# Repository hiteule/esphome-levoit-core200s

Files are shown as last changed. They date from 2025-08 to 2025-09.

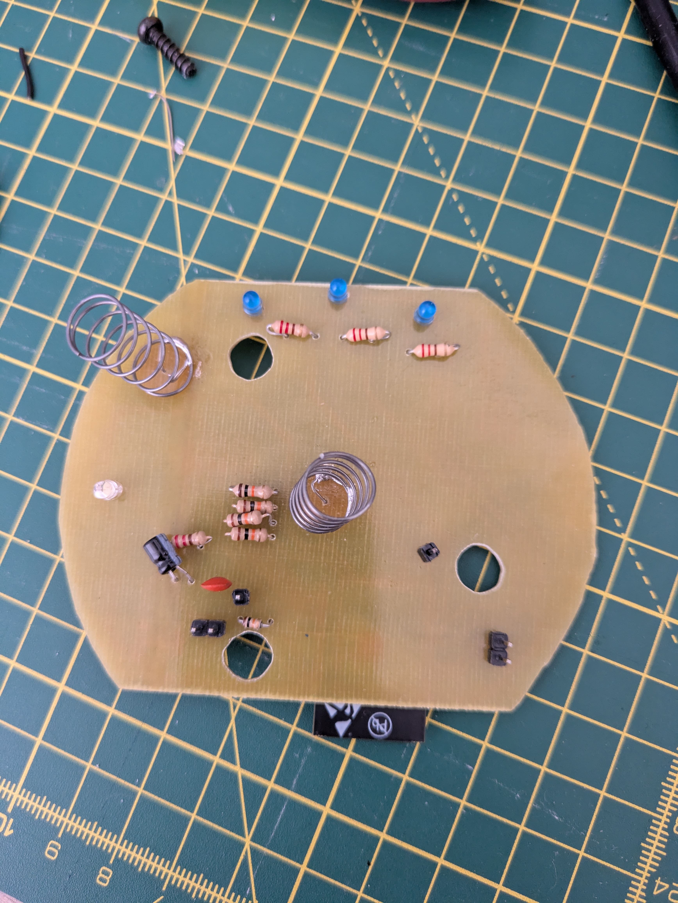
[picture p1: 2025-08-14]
pcb/pcb-front.jpg

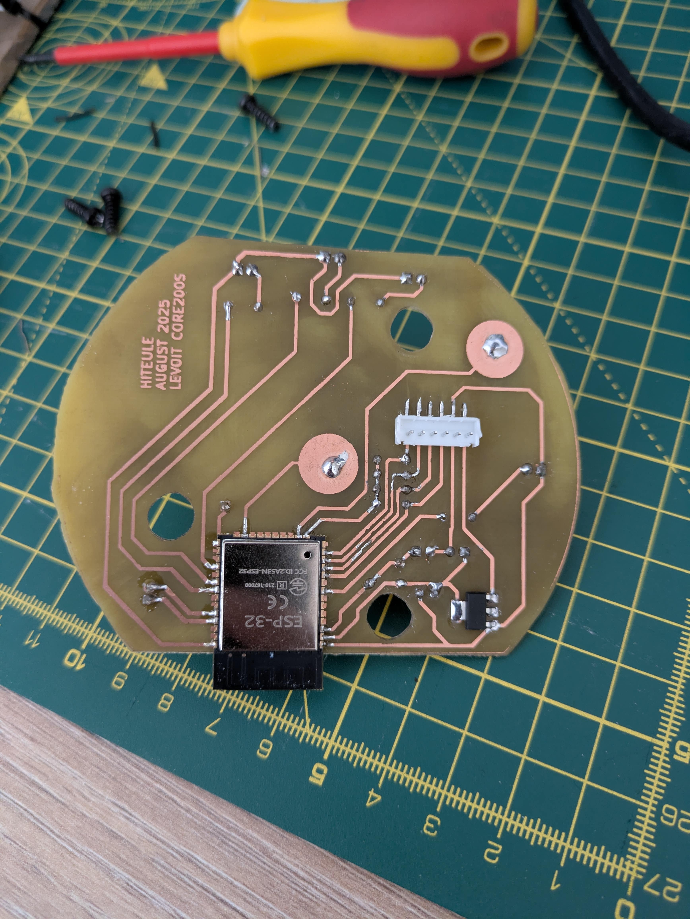
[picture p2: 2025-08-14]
pcb/pcb-back.jpg

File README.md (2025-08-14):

# ESPHome Levoit Core200s

An electronic board designed to replace the Levoit Core 200s air purifier control board (because I broke it).
Only the "Fan speed" and "Power" buttons are functional.
The air purifier is exposed via [ESPHome], which enables integration with [HomeAssistant].

## PCB

The board must be connected to the "power board" of the air purifier via the JST connector on J1.
This connector supplies 5V on pin 1. Take care to connect it the right way.

The ESP32 should be flashed with ESPHome via J2(TX), J3(RX), J6(RTS), J7(DTR) J8(3.3V), J9(GND).
For this, you can use my [ESP/Atmega programmer].

The card was designed with [Kicad]. The sources (schematic & board) are in the "pcb" folder.

## Software

The ESP32 is exposing the Air Purifier in Home Assisant. To do it, we use [ESPHome].
To do so:
* Install the ESPHome module on [HomeAssistant].
* Plug the board to your computer with J2(TX), J3(RX), J6(RTS), J7(DTR) J8(3.3V), J9(GND) and the [ESP/Atmega programmer].
* In the ESPHome module, create a new device.
* Update your ESPHome device with the `levoit-core200s.yaml` file.
* Install it on the ESP.

Now you can unplug the ESP from your computer, install it into the air purifier and connect it via J1.
ESP should boot normally and the air purifier should be visible in [HomeAssistant].

[HomeAssistant]: https://www.home-assistant.io
[ESPHome]: https://esphome.io/
[ESP/Atmega programmer]: https://github.com/hiteule/programmer-esp-atmega
[Kicad]: https://www.kicad.org

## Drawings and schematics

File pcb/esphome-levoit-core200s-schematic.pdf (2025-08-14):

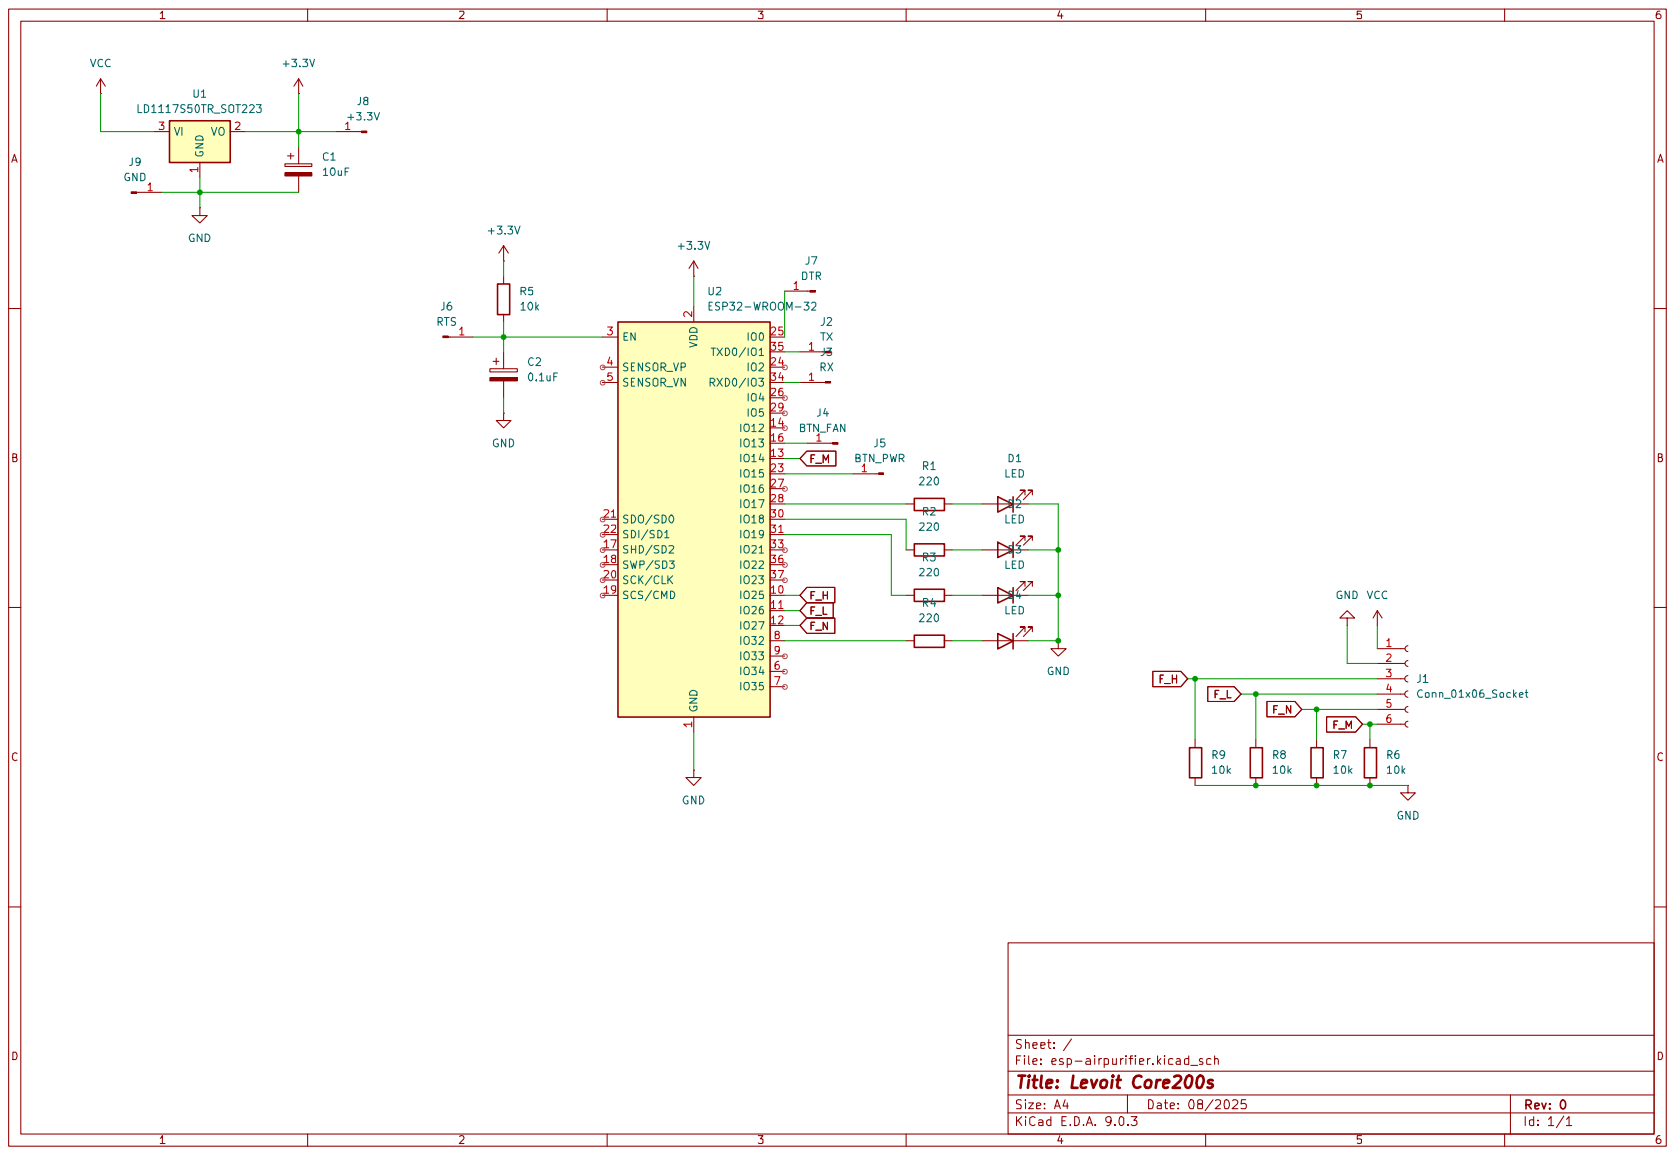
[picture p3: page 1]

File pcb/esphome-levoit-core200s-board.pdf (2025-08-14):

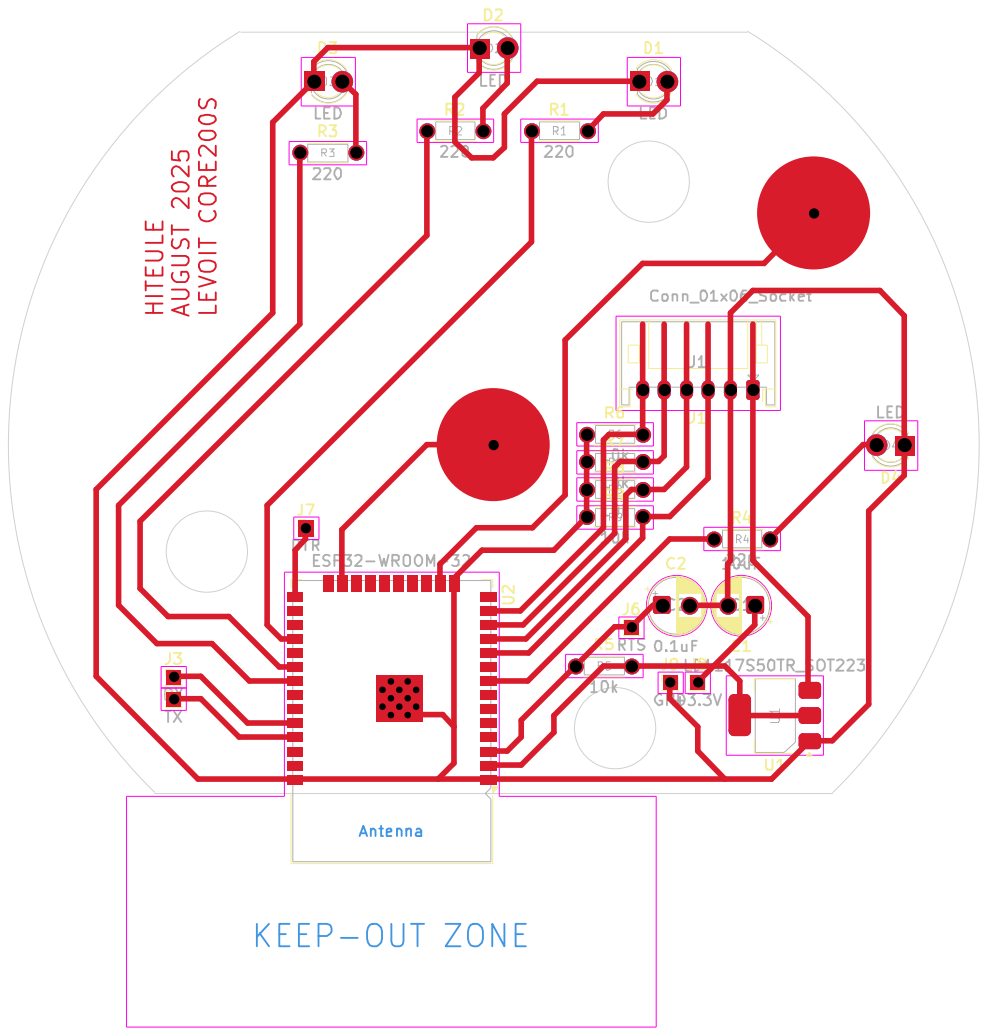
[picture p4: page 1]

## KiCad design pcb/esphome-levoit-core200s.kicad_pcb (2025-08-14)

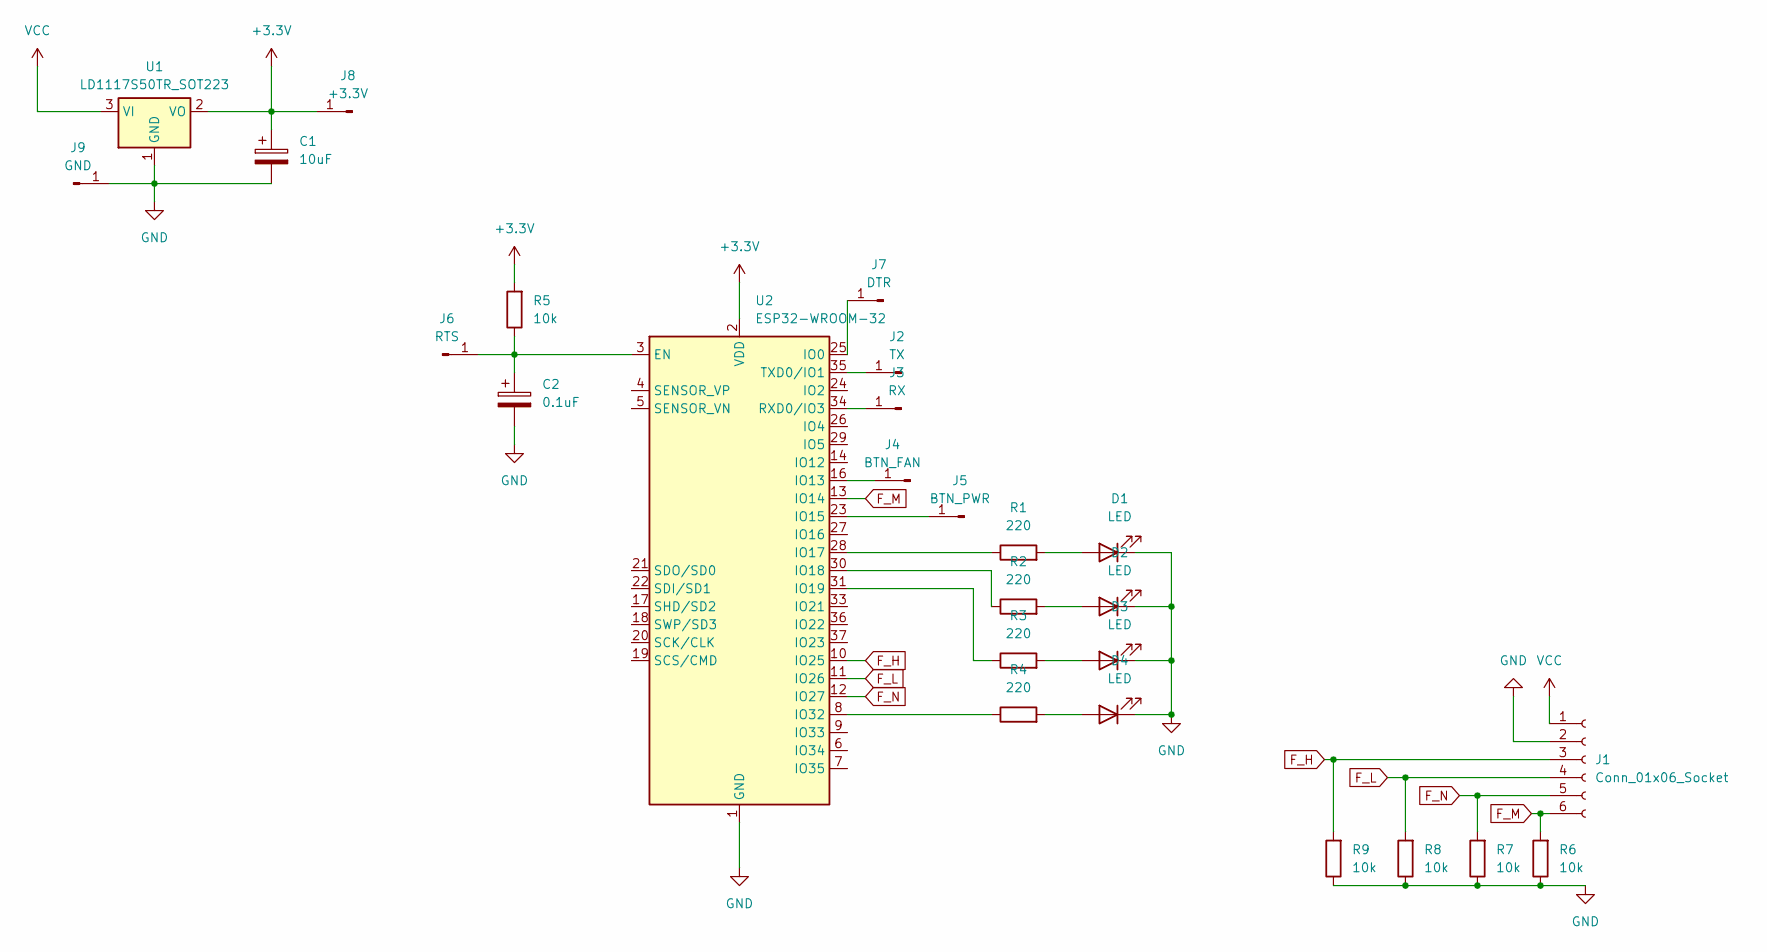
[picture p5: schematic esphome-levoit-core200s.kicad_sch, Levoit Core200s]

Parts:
C1: 10uF; CP_Radial_D5.0mm_P2.50mm
C2: 0.1uF; CP_Radial_D5.0mm_P2.50mm
D1, D2, D3, D4: LED; LED_D3.0mm
J1: Conn_01x06_Socket; JST_PH_S6B-PH-K_1x06_P2.00mm_Horizontal
J2: TX; PinHeader_1x01_P1.00mm_Vertical
J3: RX; PinHeader_1x01_P1.00mm_Vertical
J4: BTN_FAN; PinHeader_1x01_P1.00mm_Vertical
J5: BTN_PWR; PinHeader_1x01_P1.00mm_Vertical
J6: RTS; PinHeader_1x01_P1.00mm_Vertical
J7: DTR; PinHeader_1x01_P1.00mm_Vertical
J8: +3.3V; PinHeader_1x01_P1.00mm_Vertical
J9: GND; PinHeader_1x01_P1.00mm_Vertical
R1, R2, R3, R4: 220; R_Axial_DIN0204_L3.6mm_D1.6mm_P5.08mm_Horizontal
R5, R6, R7, R8, R9: 10k; R_Axial_DIN0204_L3.6mm_D1.6mm_P5.08mm_Horizontal
U1: LD1117S50TR_SOT223; SOT-223-3_TabPin2
U2: ESP32-WROOM-32

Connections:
+3.3V: C1.1, J8.1, R5.2, U1.2 (VO), U2.2 (VDD)
F_H: J1.3, R9.2, U2.10 (IO25)
F_L: J1.4, R8.2, U2.11 (IO26)
F_M: J1.6, R6.2, U2.13 (IO14)
F_N: J1.5, R7.2, U2.12 (IO27)
GND: C1.2, C2.2, D1.1 (K), D2.1 (K), D3.1 (K), D4.1 (K), J1.2, J9.1, R6.1, R7.1, R8.1, R9.1, U1.1 (GND), U2.1 (GND), U2.15 (GND), U2.38 (GND), U2.39 (GND)
unnamed: D1.2 (A), R1.2
unnamed: D2.2 (A), R2.2
unnamed: D3.2 (A), R3.2
unnamed: D4.2 (A), R4.2
unnamed: J2.1, U2.35 (TXD0/IO1)
unnamed: J3.1, U2.34 (RXD0/IO3)
unnamed: J4.1, U2.16 (IO13)
unnamed: J5.1, U2.23 (IO15)
unnamed: C2.1, J6.1, R5.1, U2.3 (EN)
unnamed: J7.1, U2.25 (IO0)
unnamed: R1.1, U2.28 (IO17)
unnamed: R2.1, U2.30 (IO18)
unnamed: R3.1, U2.31 (IO19)
unnamed: R4.1, U2.8 (IO32)
VCC: J1.1, U1.3 (VI)

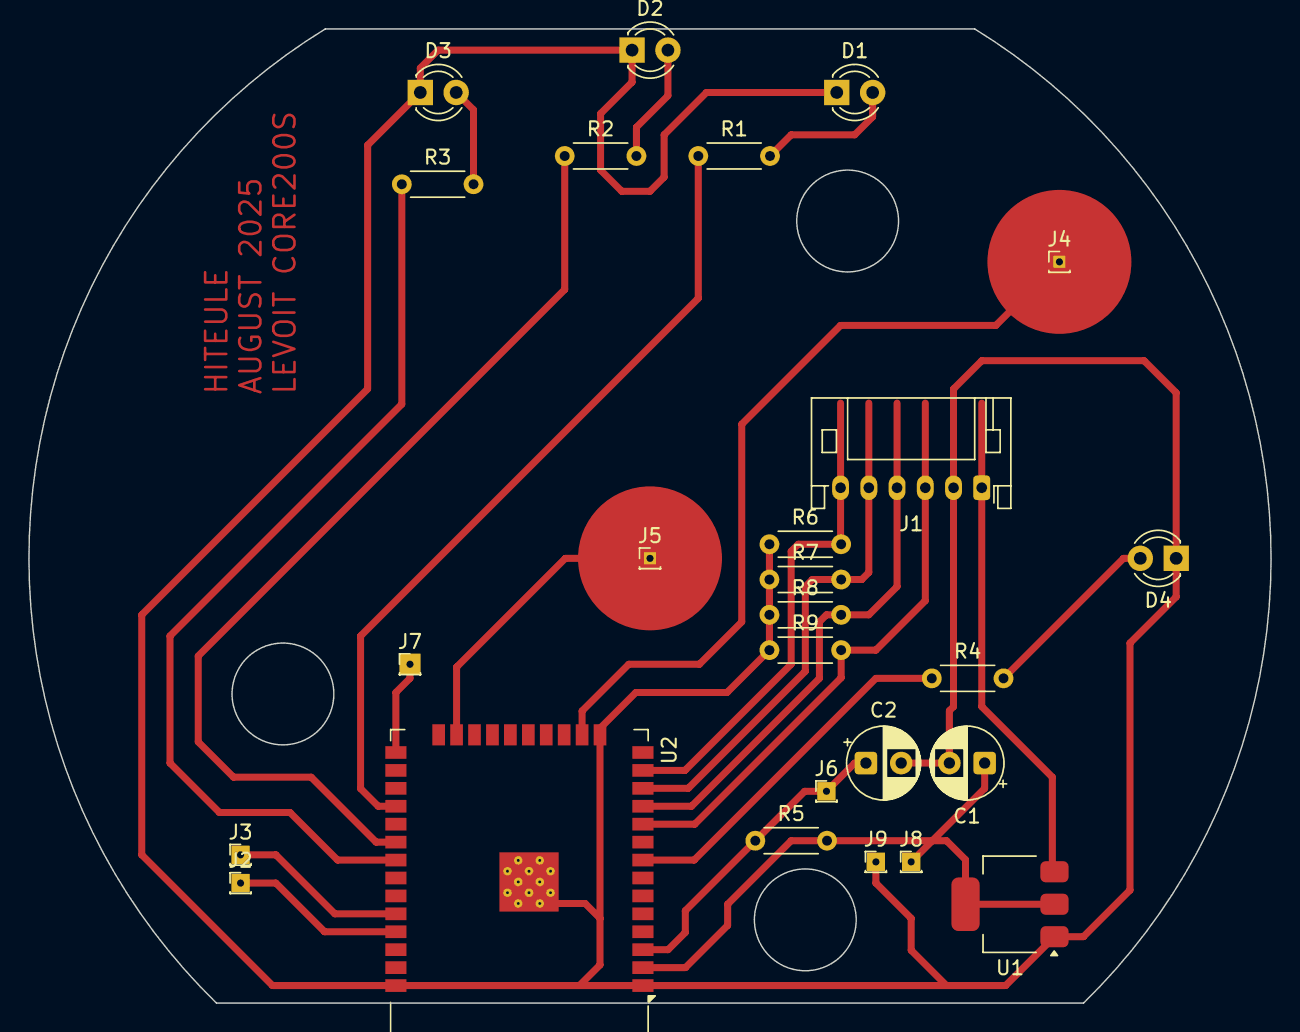
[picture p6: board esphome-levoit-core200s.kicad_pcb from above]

Board: 2 copper layers, 88.0 x 69.0 mm, 26 parts (0 on the bottom side), 21 nets.

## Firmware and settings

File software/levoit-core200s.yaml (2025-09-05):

esphome:
  name: levoit-core200s
  friendly_name: levoit-core200s

esp32:
  board: esp32dev
  framework:
    type: esp-idf

# Enable logging
logger:

# Enable Home Assistant API
api:
  encryption:
    key: "TODO"

ota:
  - platform: esphome
    password: "TODO"

wifi:
  ssid: !secret wifi_ssid
  password: !secret wifi_password

  # Enable fallback hotspot (captive portal) in case wifi connection fails
  ap:
    ssid: "Levoit Core200s Fallback Hotspot"
    password: "TODO"

captive_portal:


external_components:
  - source:
      type: git
      url: https://github.com/hiteule/esphome-levoit-core200s
      ref: master
    components: [ levoit-core200s ]

levoit-core200s:

fan:
  - platform: levoit-core200s
    id: fan_levoit_core200s
    name: Air Purifier
    pin_night: 27
    pin_low: 26
    pin_medium: 14
    pin_high: 25
    pin_led_night: 32
    pin_led_low: 17
    pin_led_medium: 18
    pin_led_high: 19

esp32_touch:
  setup_mode: false

binary_sensor:
  - platform: esp32_touch
    name: "Fan speed"
    pin: GPIO13
    threshold: 1510
    id: btn_fan_speed
    on_press:
      then:
        - fan.cycle_speed:
            id: fan_levoit_core200s
            off_speed_cycle: false
  - platform: esp32_touch
    name: "Fan power"
    pin: GPIO15
    threshold: 1640
    id: btn_fan_power
    on_press:
      then:
        - fan.toggle:
            id: fan_levoit_core200s

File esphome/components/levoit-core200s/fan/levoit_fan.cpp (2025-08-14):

#include "esphome/core/log.h"
#include "levoit_fan.h"

namespace esphome {
namespace levoit {

static const char *const TAG = "levoit-core200s.fan";

void LevoitFan::setup() {
  this->pin_night_->setup();
  this->pin_night_->pin_mode(gpio::FLAG_OUTPUT);
  this->pin_night_->digital_write(false);
  this->pin_low_->setup();
  this->pin_low_->pin_mode(gpio::FLAG_OUTPUT);
  this->pin_low_->digital_write(false);
  this->pin_medium_->setup();
  this->pin_medium_->pin_mode(gpio::FLAG_OUTPUT);
  this->pin_medium_->digital_write(false);
  this->pin_high_->setup();
  this->pin_high_->pin_mode(gpio::FLAG_OUTPUT);
  this->pin_high_->digital_write(false);
  this->pin_led_night_->setup();
  this->pin_led_night_->pin_mode(gpio::FLAG_OUTPUT);
  this->pin_led_night_->digital_write(false);
  this->pin_led_low_->setup();
  this->pin_led_low_->pin_mode(gpio::FLAG_OUTPUT);
  this->pin_led_low_->digital_write(false);
  this->pin_led_medium_->setup();
  this->pin_led_medium_->pin_mode(gpio::FLAG_OUTPUT);
  this->pin_led_medium_->digital_write(false);
  this->pin_led_high_->setup();
  this->pin_led_high_->pin_mode(gpio::FLAG_OUTPUT);
  this->pin_led_high_->digital_write(false);

  this->state = false;
  this->speed = 0;
  this->publish_state();
}

void LevoitFan::dump_config() { LOG_FAN("", "Levoit Fan", this); }

fan::FanTraits LevoitFan::get_traits() {
  // 200s has 4 speeds (night, low, medium, high)
  return fan::FanTraits(false, true, false, 4);
}

void LevoitFan::control(const fan::FanCall &call) {
  bool newPowerState = this->state;

  if (call.get_state().has_value()) {
    newPowerState = *call.get_state();
    
    if (newPowerState) {
      // power on
      this->setFanOff();
      this->pin_low_->digital_write(true);
      this->state = true;
      this->speed = 1;
    } else {
      // power off
      this->setFanOff();
      this->state = false;
      this->speed = 0;
    }
  }

  if (call.get_speed().has_value()) {
    uint8_t targetSpeed = *call.get_speed();

    switch (targetSpeed) {
      case 0:
        // send power off
        this->setFanOff();
        this->state = false;
        this->speed = 0;
        break;
      case 1:
        // speed 1
        this->setFanOff();
        this->pin_night_->digital_write(true);
        this->pin_led_night_->digital_write(true);
        this->state = true;
        this->speed = 1;
        break;
      case 2:
        // speed 2
        this->setFanOff();
        this->pin_low_->digital_write(true);
        this->pin_led_low_->digital_write(true);
        this->state = true;
        this->speed = 2;
        break;
      case 3:
        // speed 3
        this->setFanOff();
        this->pin_medium_->digital_write(true);
        this->pin_led_medium_->digital_write(true);
        this->state = true;
        this->speed = 3;
        break;
      case 4:
        // speed 4
        this->setFanOff();
        this->pin_high_->digital_write(true);
        this->pin_led_high_->digital_write(true);
        this->state = true;
        this->speed = 4;
        break;
    }
  }

  this->publish_state();
}

void LevoitFan::setFanOff() {
  this->pin_night_->digital_write(false);
  this->pin_low_->digital_write(false);
  this->pin_medium_->digital_write(false);
  this->pin_high_->digital_write(false);
  this->pin_led_night_->digital_write(false);
  this->pin_led_low_->digital_write(false);
  this->pin_led_medium_->digital_write(false);
  this->pin_led_high_->digital_write(false);
}

}  // namespace levoit
}  // namespace esphome
